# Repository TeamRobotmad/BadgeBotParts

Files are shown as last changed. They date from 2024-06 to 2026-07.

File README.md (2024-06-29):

# BadgeBotParts
Related documents and CAD files for BadgeBot - a small robot based on the [EMF Camp 2024 Badge](https://tildagon.badge.emfcamp.org/)

Buy at https://robotmad.odoo.com/

The motors, wheels & ball caster come from [Pololu](https://www.pololu.com), available from other ditributors as well like [Technobots](https://www.technobots.co.uk) and the [PiHut](https://thepihut.com).
+ https://www.pololu.com/product/952
+ https://www.pololu.com/product/1088
+ https://www.pololu.com/product/1098

# Hexpansion EEPROM Recovery #
If you have issues with any hexpansion which contains an app on its EEPROM causing the Badge S/W to crash you can erase the EEPROM by following the instructions in [hexpansion_eeprom_recovery](https://github.com/TeamRobotmad/BadgeBotParts/blob/main/Docs/hexpansion_eeprom_recovery.pdf)

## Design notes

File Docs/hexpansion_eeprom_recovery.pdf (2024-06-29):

### emfcamp/badge-2024 Hexpansion EEPROM Recovery

If you have issues with a HexDrive, or for that matter any hexpansion fitted with an EEPROM, e.g. a software incompatibility with a particular badge software version, you can reset the EEPROM back to blank as follows:

1. Plug in the hexpansion to Slot 1 (will work with any slot but you have to change the "1" below to the slot number.
2. Connect your favourite Terminal program to the COM port presented by the Badge over USB.
3. Press "Ctrl" & "C" simultaneously. i.e. "Ctrl-C"
4. You should now be presented with a prompt ">>>" which is called the python REPL. At this type in the following lines (the HexDrive EEPROM is 8kbytes so requires 16 bit addressing, hence the addrsize=16 other hexpansions may use smaller EEPROMS where this is not required):

from machine import I2C
i = I2C(1)
i.writeto_mem(0x50, 0, bytes([0xFF]*8192), addrsize=16)
5. As long as there is no Traceback then this worked. But you can check by reading back the EEPROM contents with:

i.readfrom_mem(0x50,0,32,addrsize=16)

You should get a response which confirms that the first 32 bytes have been reset back to 0xFF:
b'\xff\xff\xff\xff\xff\xff\xff\xff\xff\xff\xff\xff\xff\xff\xff\xff\xf f\xff\xff\xff\xff\xff\xff\xff\xff\xff\xff\xff\xff\xff\xff\xff'

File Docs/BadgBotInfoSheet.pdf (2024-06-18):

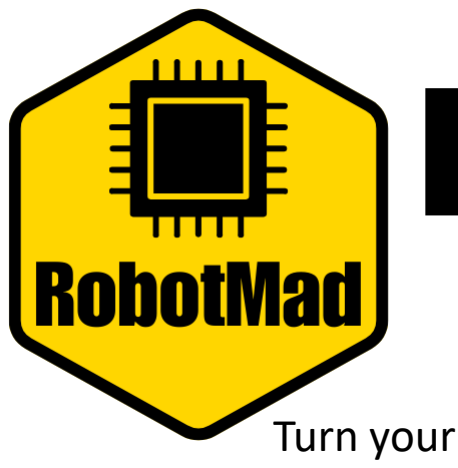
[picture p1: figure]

# BadgeBot

Turn your EMF 2024+ Badge into a Robot!

Using the RobotMad Hex-Drive Hexpansion, and 3D
printed motor mounts.

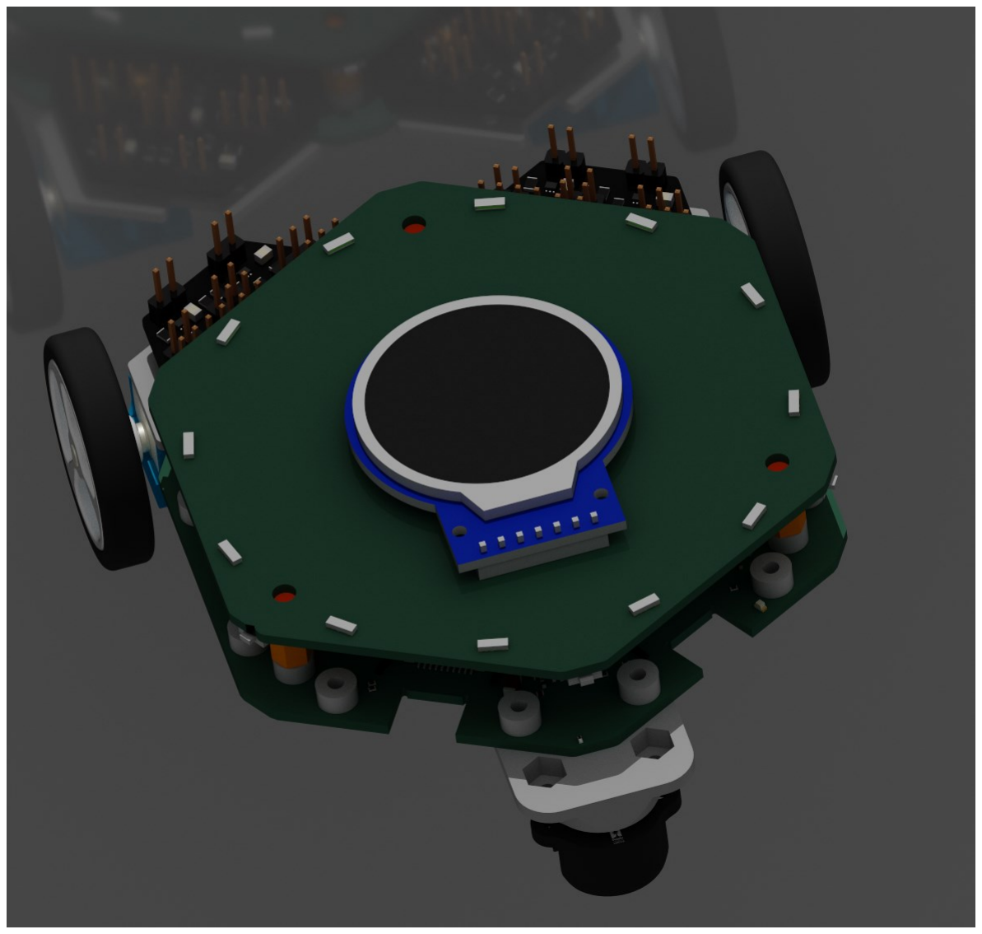
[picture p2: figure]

Designed for n20 micro gear motors, Pololu 32mm wheels, and ball caster.

https://www.pololu.com/category/60/micro-metal-gearmotors

https://www.pololu.com/product/952 https://www.pololu.com/product/1088

Mount the system to the underside of your badge using one pair of m2 mounting holes, pair A for the motor pointing straight out the side. Pair B or C for angled motor mounting, this will include one of the motor mount top part holes and will need a longer m2 bolt.

| Here is an example of a motor mount set up using the C pair of holes lined up with the expansion mounting holes of the badge, while one bolt also holds the mo- tor mount.

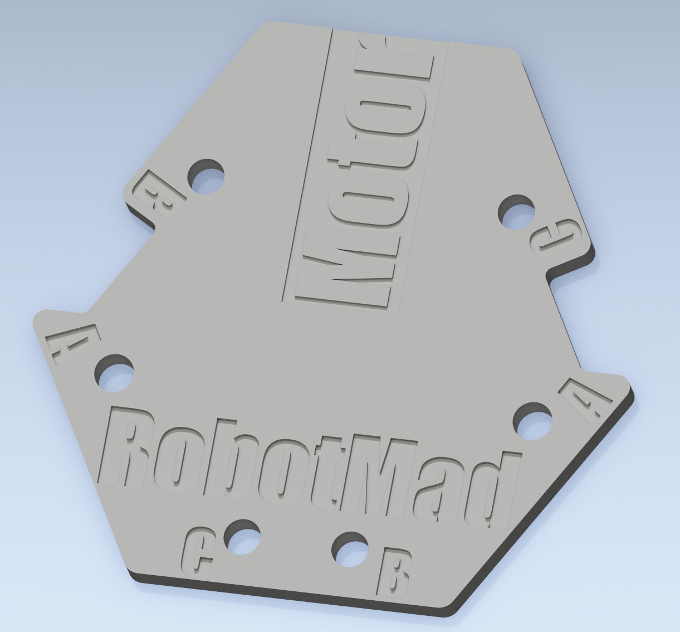
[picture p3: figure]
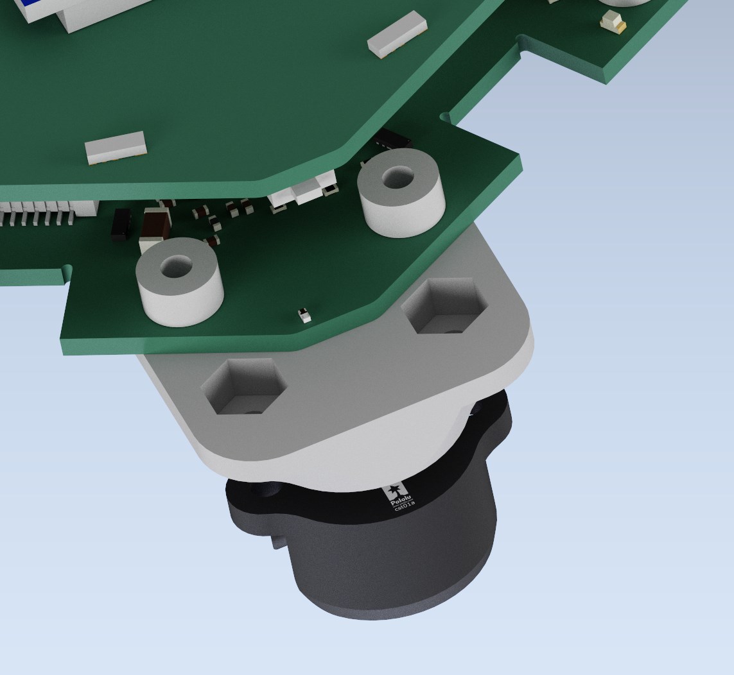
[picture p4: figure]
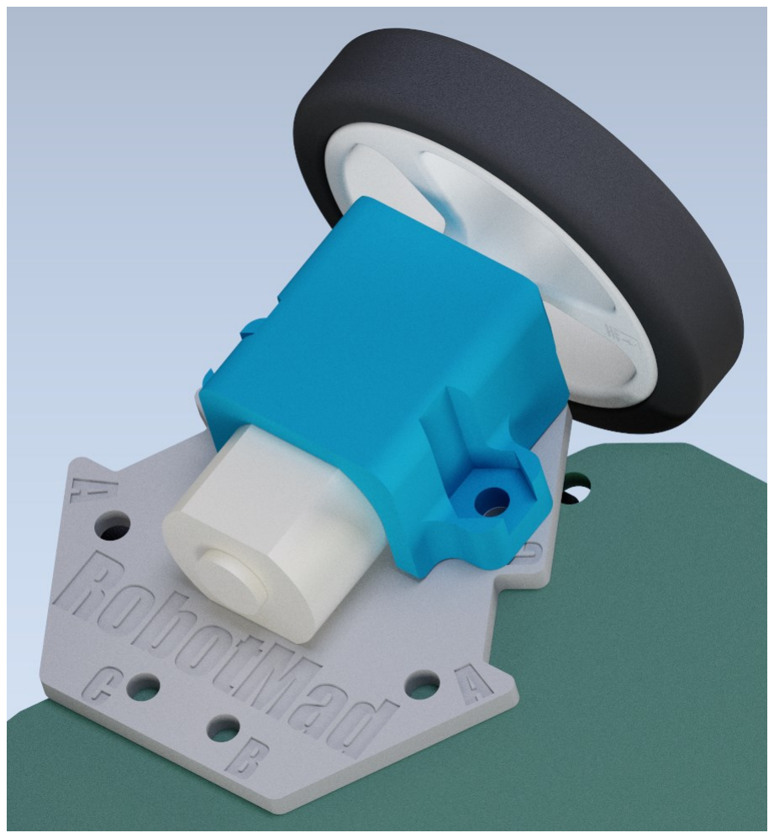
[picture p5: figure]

The ball caster mounts across a corner of the badge using the adjacent hexpansion mounts.

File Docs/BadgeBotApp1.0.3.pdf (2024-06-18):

BadgeBot App V1.0.3 Instructions.

For use with Badge FW 1.7.0 (follow official guidance to update and connect to home network Wi-Fi https://tildagon.badge.emfcamp.org/using-the-badge/end-user-manual/)

Install on the Badge via options—App store, StoreInstall, BadgeBot.

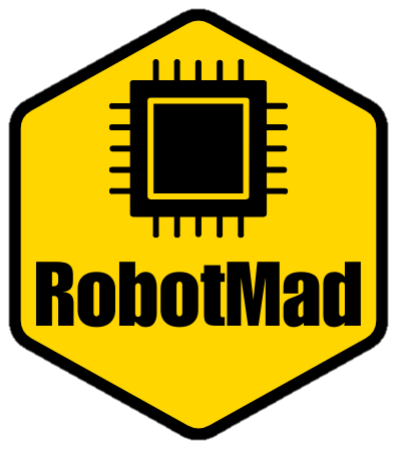
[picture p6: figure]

Navigate to BadgeBot app, On the first time run expect to need to flash the EEPROM on the Hex-Drive hexpansion.

This allows the hexpansion to be automatically recognised. This means you need to not have any other hexpansions plugged in to your badge during the EEPROM flashing process. If built the same as BadgeBot instructions the HexDrive hexpation should come up as in slot 3, with the BadgeBot app giving the following message. “Hexpansion Detected in (Slot 3) init EEPROM as HexDrive”

Press C to accept.

Next the app will prompt to install the Hex-drive app onto the hexpansion,

“HexDrive detected in Slot 3, Upgrade HexDrive App?”

Press C to accept. The app will then need you to “reboop” your badge using the button on the base badge board, labelled on the underside. The first time set-up is now complete.

Navigate back to the BadgeBot app.

The app will tell you to press C to begin programming your movement sequence.

Create your program using buttons A, B,D, and E.

Run using a long press of button C.

Set the badge down during the 5 second count down and watch it go!

After the program has run you can run the same program again by pressing C or restart the programming process using F.

Enjoy experimenting with the movement program.

The App code is open source on GitHub, try adding your own functionality!

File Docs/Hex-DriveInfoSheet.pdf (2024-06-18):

# RobotMad Hex-Drive

A Motor and servo drive hexpansion for the EMF Badge.

## Featuring:

### 3 power source options

### 2 Motor drivers

### Up to 4 servo outputs

### Adjustable 5V power supply

### (max 12v)

### 64K bit EEPROM

### Easy to modify 0805 based design

## Power Options

The Hex-Drive supports badge supplied power, 1 cell external battery, or 2 cell external battery.

Badge power is selected by default using a copper track on the back of the board.

To select an external power source, the track between +BADGE and +LV must be cut carefully along the line indicated “CUT” between the white marked lines.

Then using header pins and a jumper connect +BAT to +LV for a 1 cell battery, or +BAT to +HV for a 2 cell battery. The battery should be connected to the BAT pins just to the side of the selector pins. TAKE CARE ABOUT POLARITY

You can return to Badge supplied power by connecting +BADGE to +LV again.

## Motors and Servos

There are 2 separate motor drivers and outputs. M1, M2.

4 servo outputs, S1, S2, S3, S4.

All of these outputs accept standard 2.54mm pitch header pins

To use a servo you have to not be using its corresponding motor. S1 and S2 correspond to M1, S3 and S4 correspond to M2.

If only using motors, it is beneficial to add some large though hole capacitors to the board using the servo power connection

## Adjustable Power supply

The power supply is adjustable by changing the feedback voltage divider resistors R1 and R2. we recommend only changing R2, changing C2 and C3 is recommended when changing voltage. Additional capacitors added to power points on the board is always beneficial to voltage stability.

When on badge power current limit is 300mA at 5V.

On single cell lipo, max current is 900mA

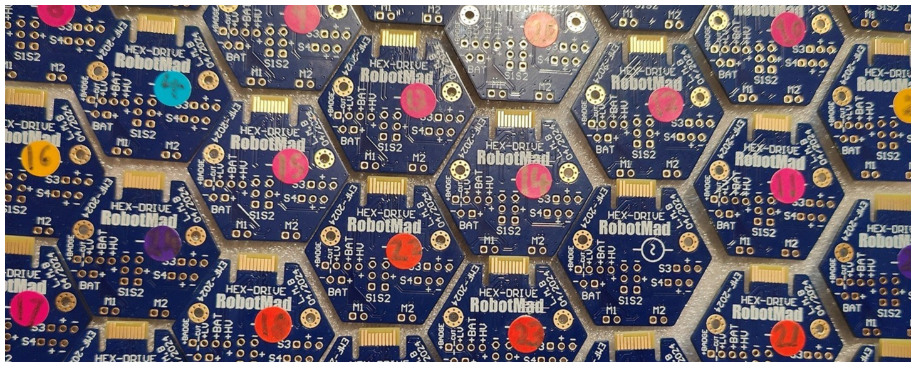
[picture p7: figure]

Below is values for 5V (default), 6V and 12V.

Vout | R2 | C3 | C2
5 | 30k | 1.8nF | 22uF
6 | 37.4k | 1.5nF | 30uF
12 | 86.6k | 560pF | 47uF

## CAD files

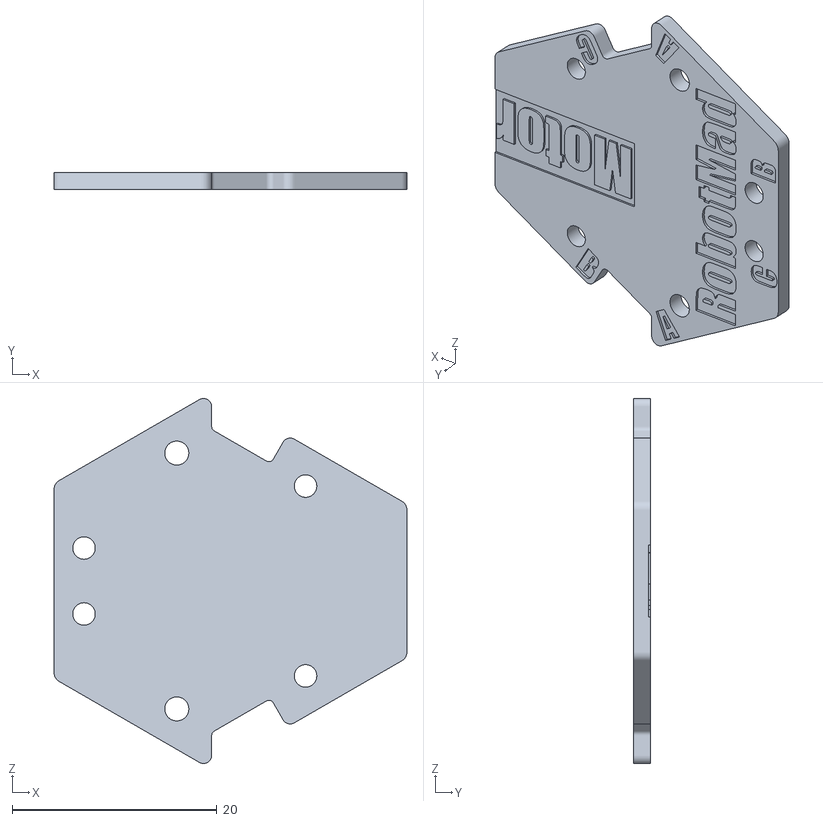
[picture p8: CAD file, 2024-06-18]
STL files/motormountV2.stl
34.5 x 1.70 x 35.7

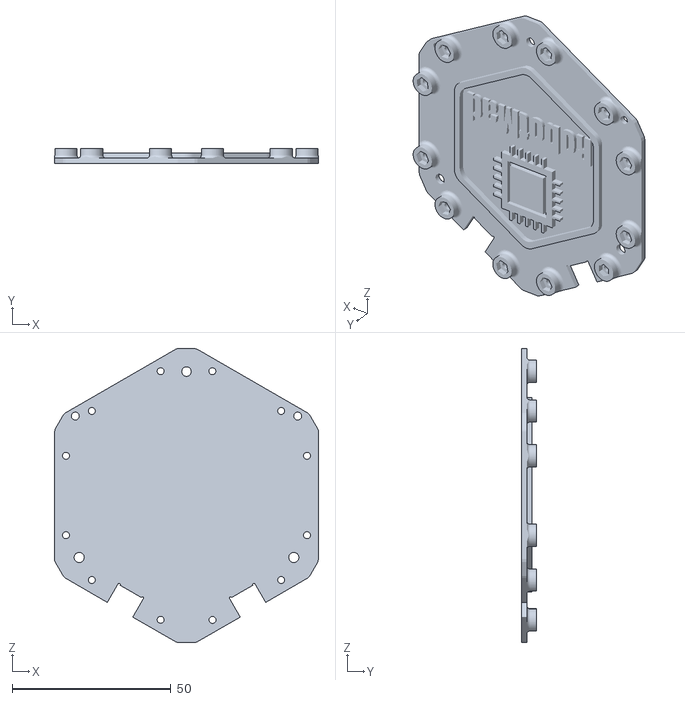
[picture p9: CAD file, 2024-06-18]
STL files/fakebadgeV1.stl
83.1 x 4.60 x 92.5

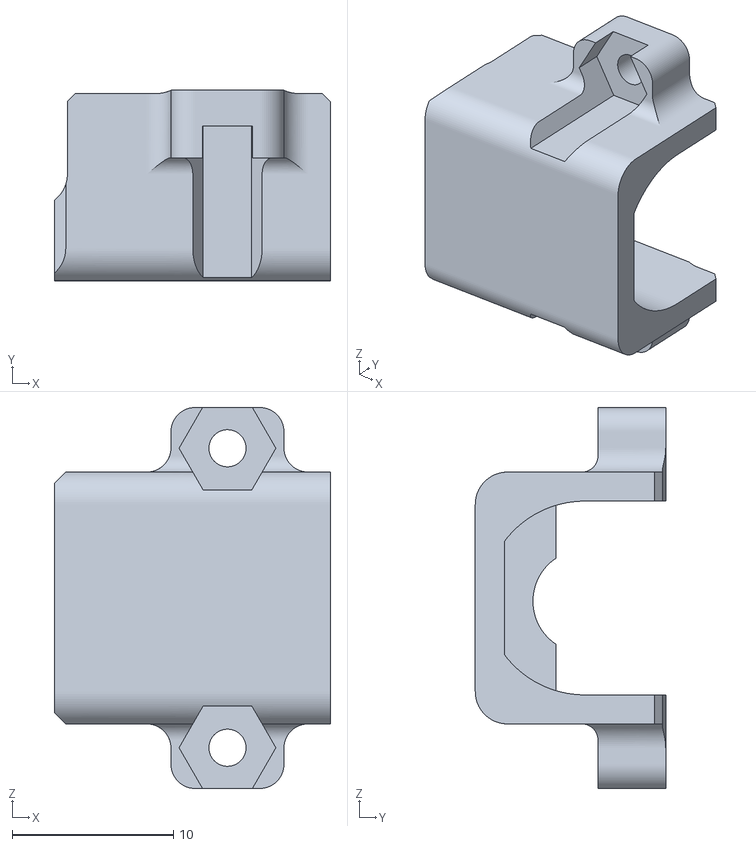
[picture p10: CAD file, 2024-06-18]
STL files/MotorTopV2.stl
17.1 x 11.8 x 23.6

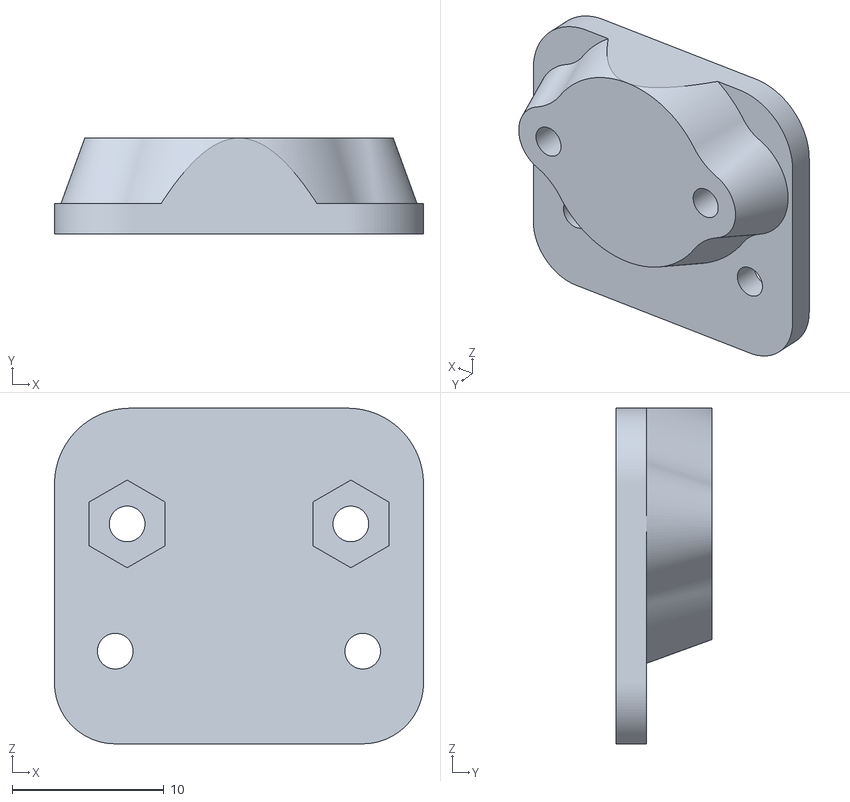
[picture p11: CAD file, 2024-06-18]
STL files/ball-mountV1.5.stl
24.3 x 6.30 x 22.1

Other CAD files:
CAD files/MotorTop.ipt
CAD files/ball-mount.ipt
CAD files/motormount.ipt

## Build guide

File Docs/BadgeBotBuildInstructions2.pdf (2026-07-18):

# BadgeBot Kit Parts list

## HexDrive-V2

1x

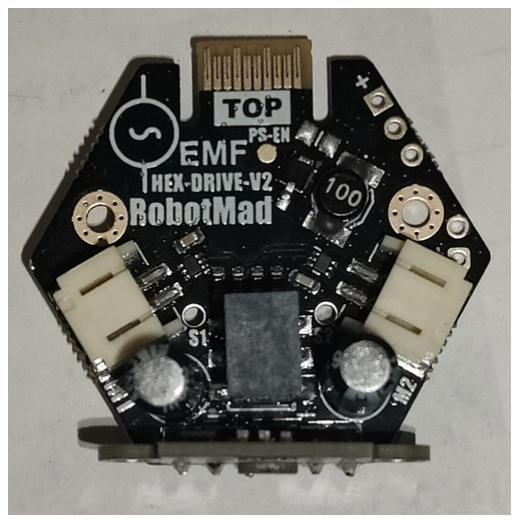
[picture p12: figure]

## LED Shroud

1x

## Short Screw m2-5mm

8x

## Long Screw m2-8mm

2x

## Motor top bracket

2x

## Mounting plate

2x

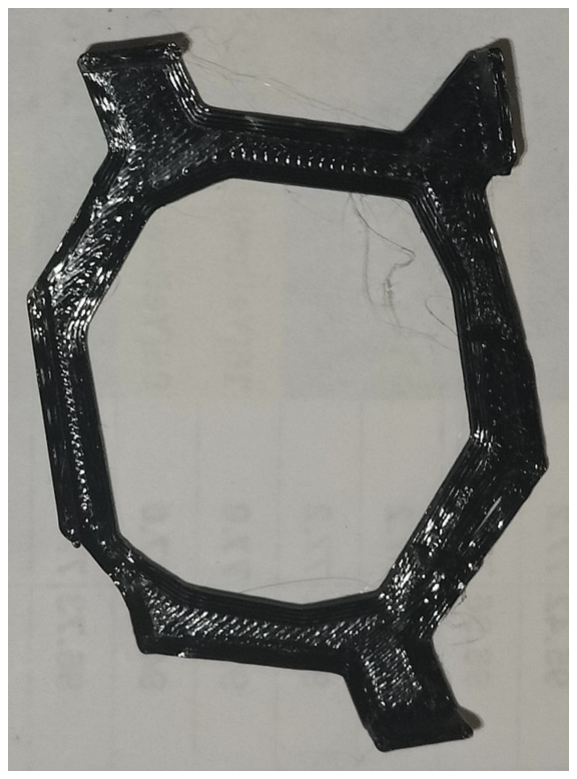
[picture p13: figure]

## Motor

2x

## Left – Yellow & Orange Right – Blue & Green

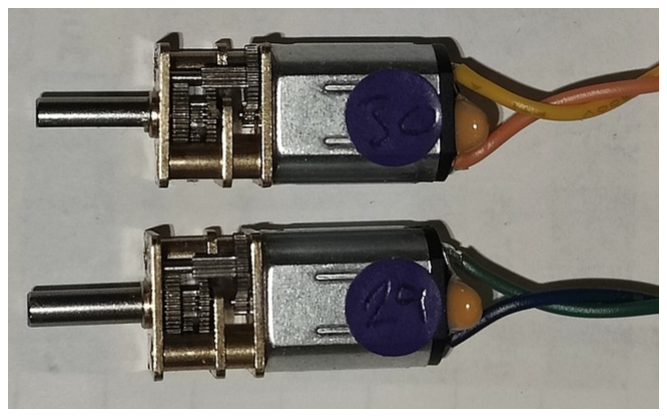
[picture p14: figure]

## Cable Clip

1x

## Free Gift, Badge Battery holder - 1x

## Nut m2

2x

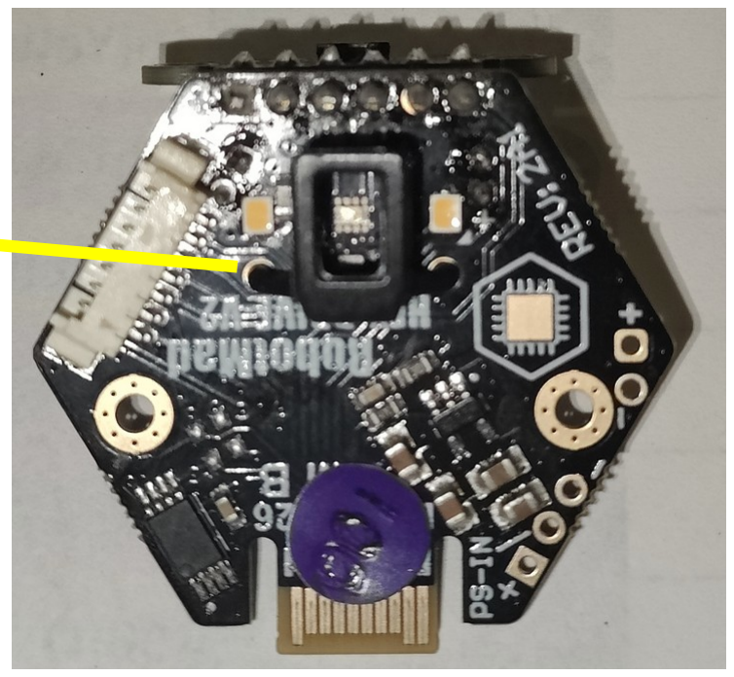
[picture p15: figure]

1. Insert the small ‘LED shroud’ piece into the 2

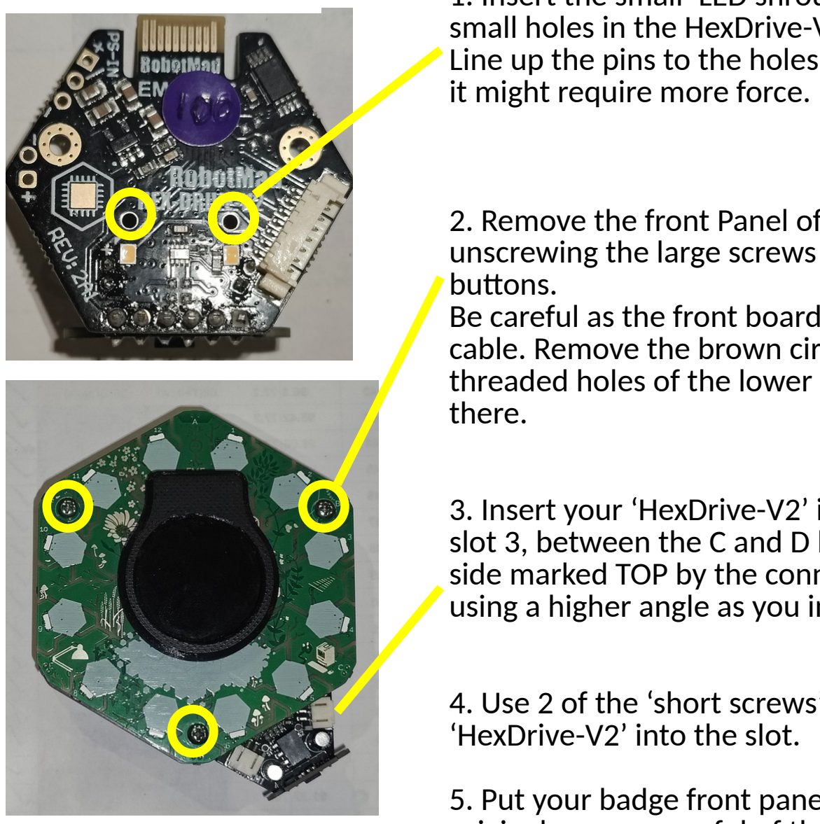
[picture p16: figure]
it might require more force.; buttons.; there.; ‘HexDrive-V2’ into the slot.

small holes in the HexDrive-V2, facing the front. Line up the pins to the holes and push carefully but

2. Remove the front Panel of your badge by unscrewing the large screws by the B, D, and F
Be careful as the front board is still attached via flex cable. Remove the brown circles covering the threaded holes of the lower board if they are still

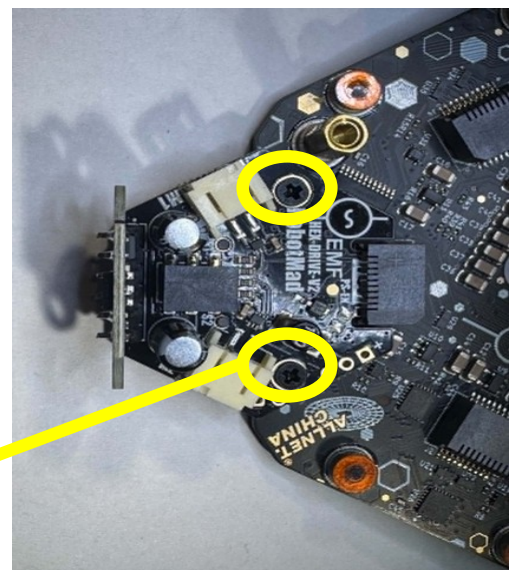
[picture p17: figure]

3. Insert your ‘HexDrive-V2’ into the hexpansion slot 3, between the C and D buttons. Make sure the side marked TOP by the connector is facing up. Try using a higher angle as you insert into the slot.
4. Use 2 of the ‘short screws’ to secure the

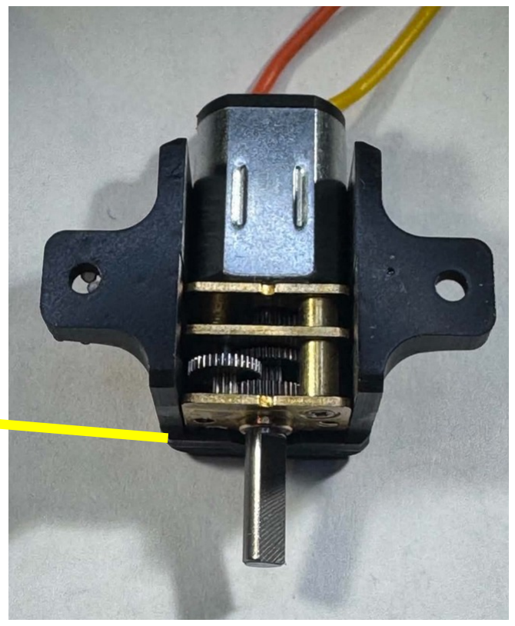
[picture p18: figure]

5. Put your badge front panel back on using its original screws, careful of the flex cable.
6. Turn your badge over, careful of the screen.
7. Line up one of the ‘mounting plates’ to the badge over the slot to the left of the ‘Hex-Drive-V2’. Use a ‘short screw’ in the hole labelled L into the hole closer to the ‘HexDrive-V2’.
8. Place the ‘motor’ with the orange and yellow wires, inside the ‘motor top bracket’ with the gearbox up against but inside the small wall at one end.
9. Place the ‘motor top bracket’ with the ‘motor’. Over the raised platform of the ‘mounting plate’ Matching and lining up with the ML and MR holes.
10. Screw a ‘long screw’ though the hole marked ML, though the ‘motor top bracket’, ‘mounting plate’ and into the badge’s other mounting hole for this hexpansion slot.

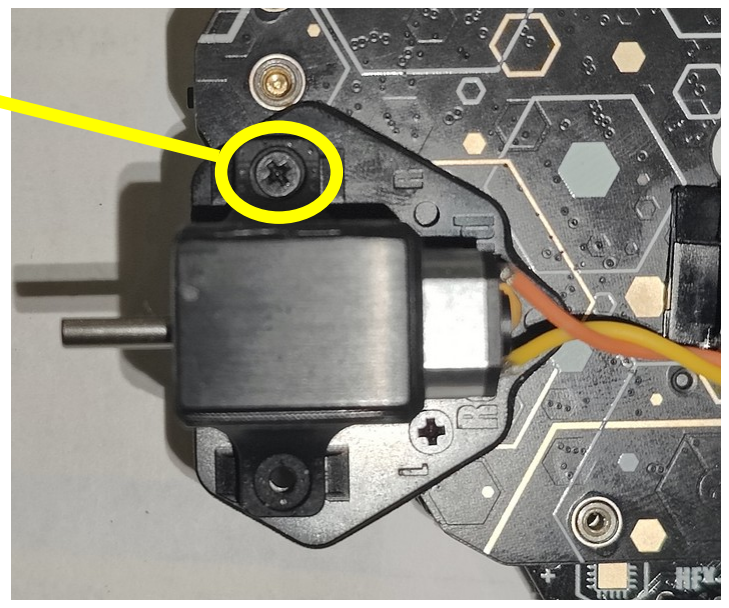
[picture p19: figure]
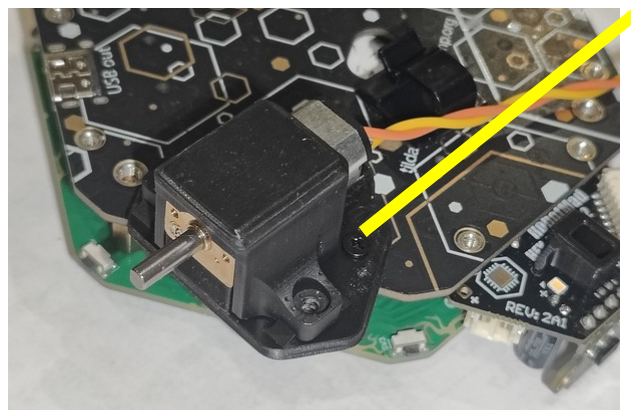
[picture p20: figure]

11. Use a ‘short screw’ in the hole marked MR while holding a ‘nut’ on the other side of the ‘mounting plate.’

BadgeBot build instructions.

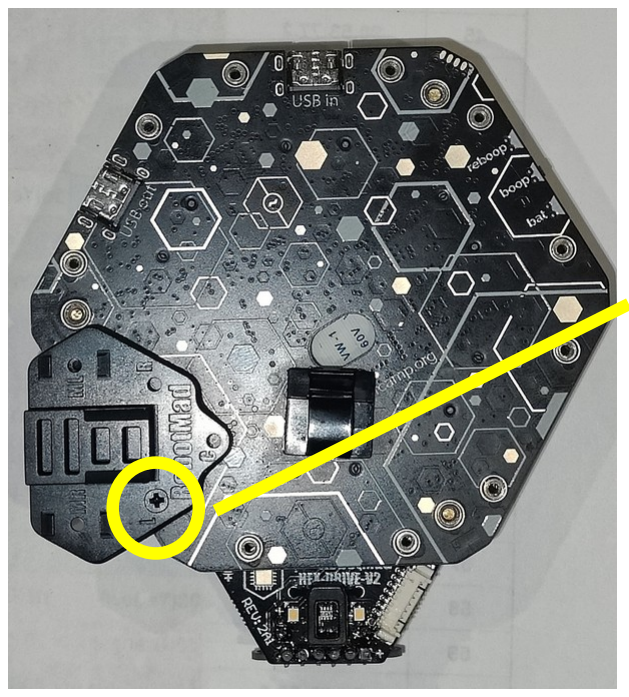
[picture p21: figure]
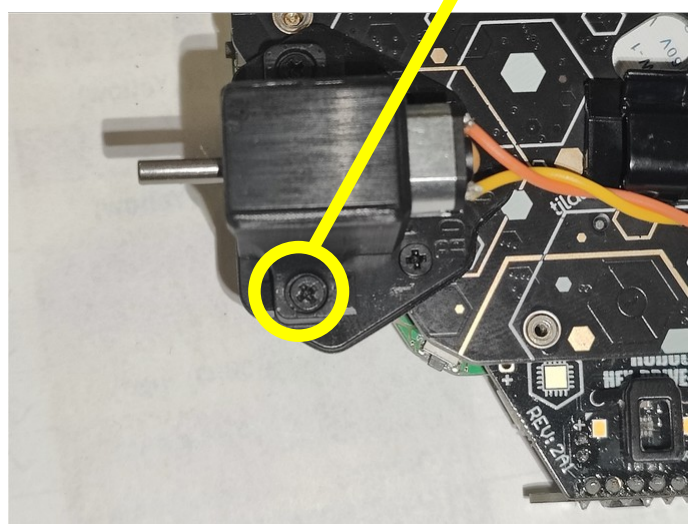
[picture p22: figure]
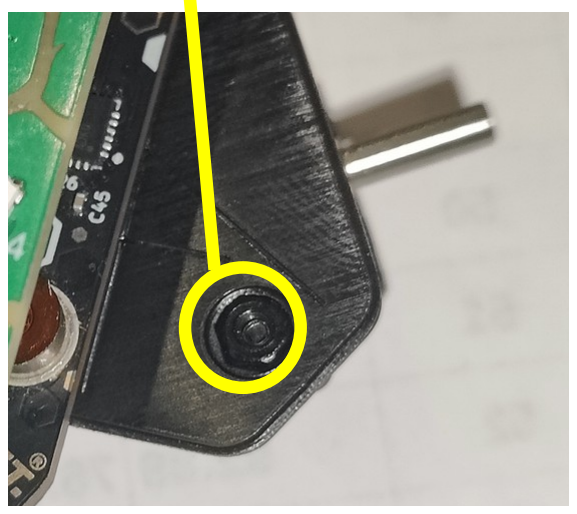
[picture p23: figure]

BadgeBot build instructions.

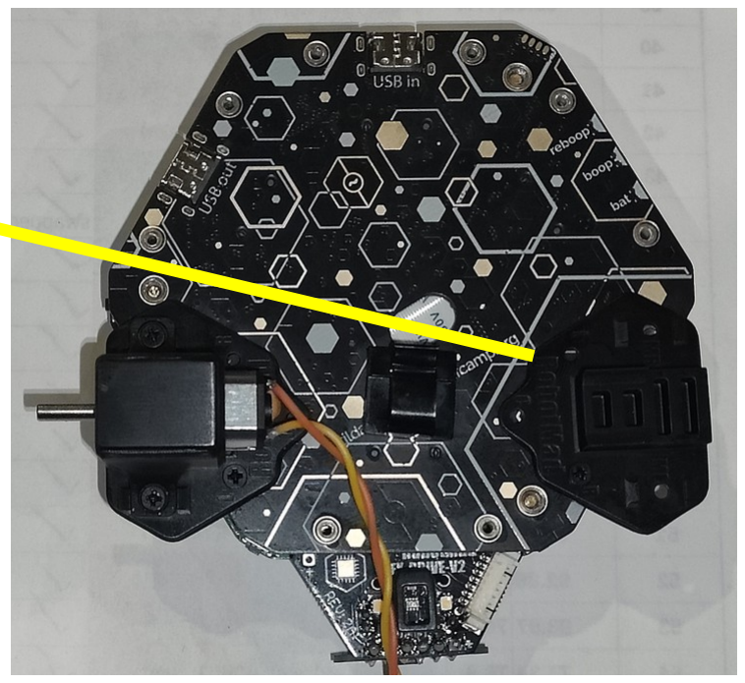
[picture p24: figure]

12. Line up the other ‘mounting plate’ to the badge over the slot to the right of the ‘Hex-Drive-V2’. Use a ‘short screw’ in the hole labelled R into the hole closer to the ‘HexDrive-V2’

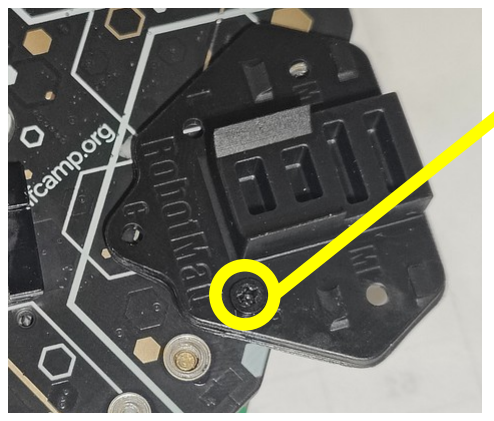
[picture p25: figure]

8. Place the ‘motor’ with the green and blue wires, inside the other ‘motor top bracket’ with the gearbox up against but inside the small wall at one end.

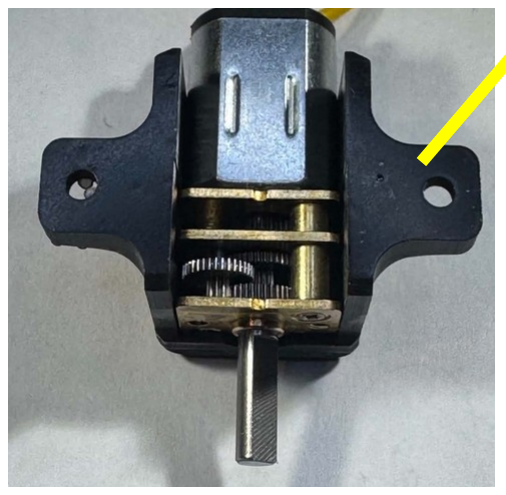
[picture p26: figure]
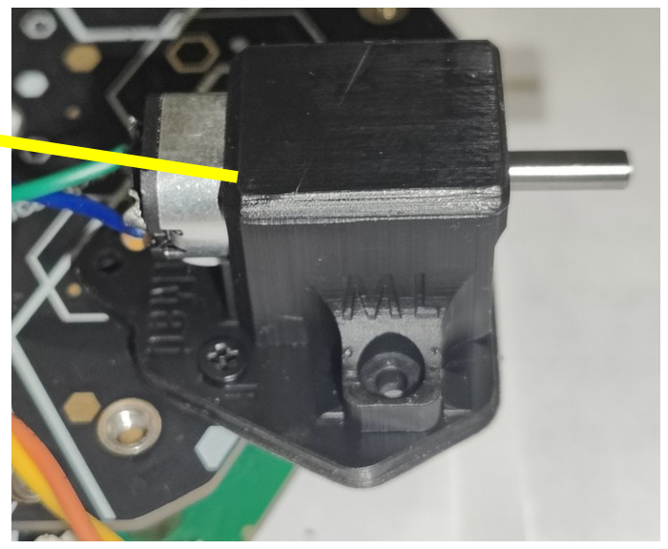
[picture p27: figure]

9. Place the ‘motor top bracket’ with the ‘motor’. Over the raised platform of the ‘mounting plate’ Matching and lining up with the ML and MR holes.
15. Screw a ‘long screw’ though the hole marked MR, though the ‘motor Top bracket’, ‘mounting plate’ and into the badge’s other mounting hole for this hexpansion slot.

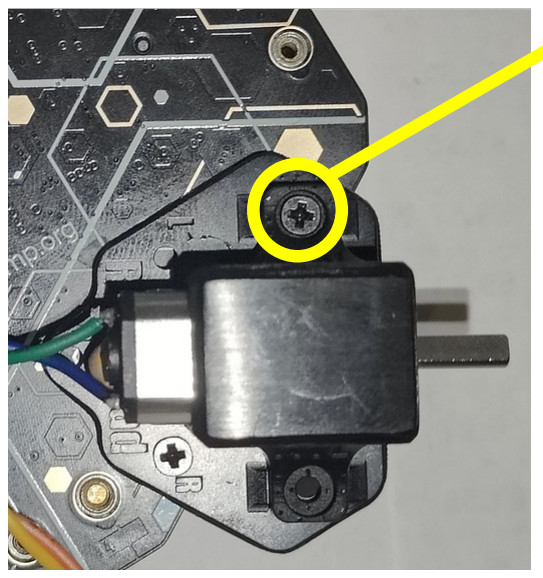
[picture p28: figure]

16. Use a ‘short screw’ in the hole marked ML while holding a ‘nut’ on the other side of the ‘mounting plate’.
17. Plug in the ‘motors’ to the ‘HexDrive-V2’ crossing the wires over for the neatest connection. The connectors are rather tight and polarised with a notch at the top. Orange and yellow into ‘M1’. Blue and green into ‘M2’.
18. Take off the backing and place the ‘cable clip’ just above the hole in the badge main board, in line between the 2 motors. Then insert the wires from the motors to keep them tidy.
19. Use 2 ‘small screws’ in the holes on the ‘ball mount’ marked S, lined up to the holes of the hexpantion slot between buttons F and A. Under the USB in port.

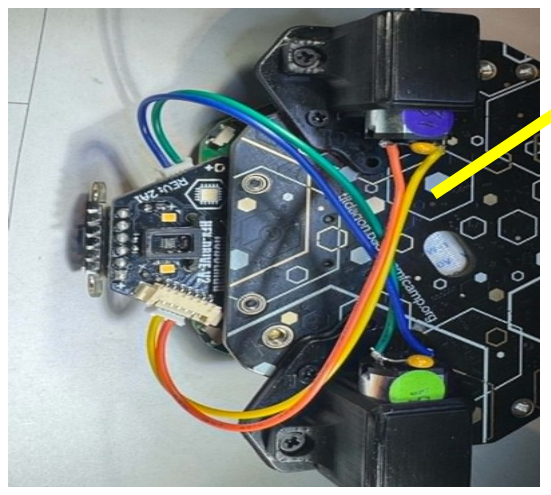
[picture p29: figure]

20. Push the ‘wheels’ onto the motor shafts, flat side out, by lining up the flat side of the shaft with the flat in the wheels hole.

Your BadgeBot is complete! You can now install the BadgeBot app from the Badge’s app store.

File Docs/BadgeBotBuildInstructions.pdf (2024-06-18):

BadgeBot build instructions.

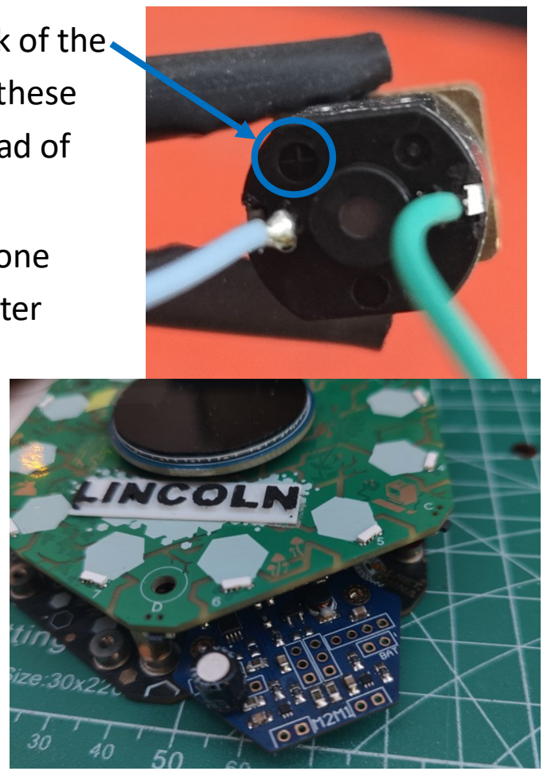
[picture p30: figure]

1. Solder wirers to the motors. Notice the + mark on the back of the motor. Colour coded in these instructions for connivance as these do matter ort your robot may go backward or in circles instead of forwards.

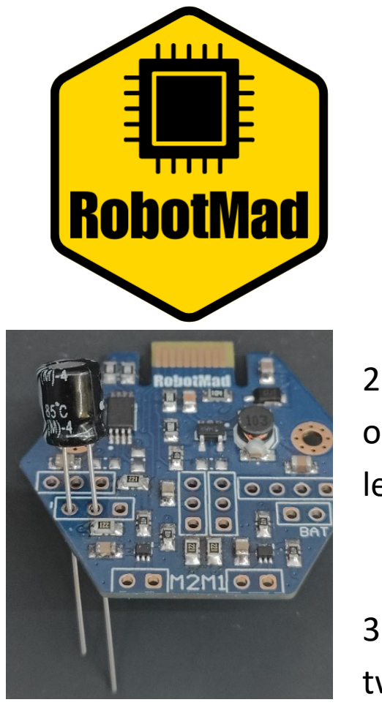
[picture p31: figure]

2. Solder the optional but recommended additional capacitor to one of the servo outputs. Note the polarity, grey line on cap and shorter leg go to the negative marked hole.
3. Insert the HexDrive hexpansion into the slot on the badge between the C and D buttons.

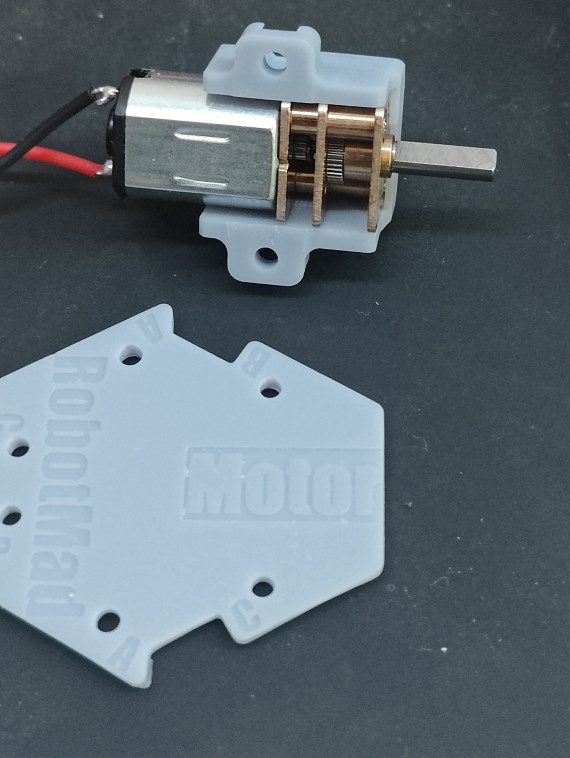
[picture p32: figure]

4. Insert the motors into the motor mounting pieces. Then place on the mounting bracket over the “Motor” text.

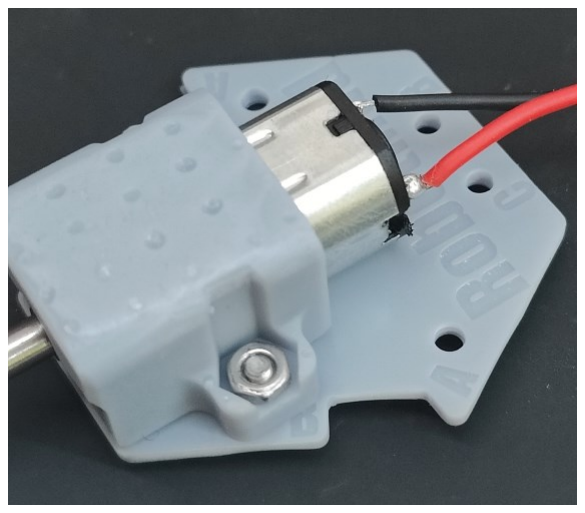
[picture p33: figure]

5. bolt the motor down using a small m2 bolt and nut, though the ‘B’ hole. Do not do the other side of the motor mount yet.

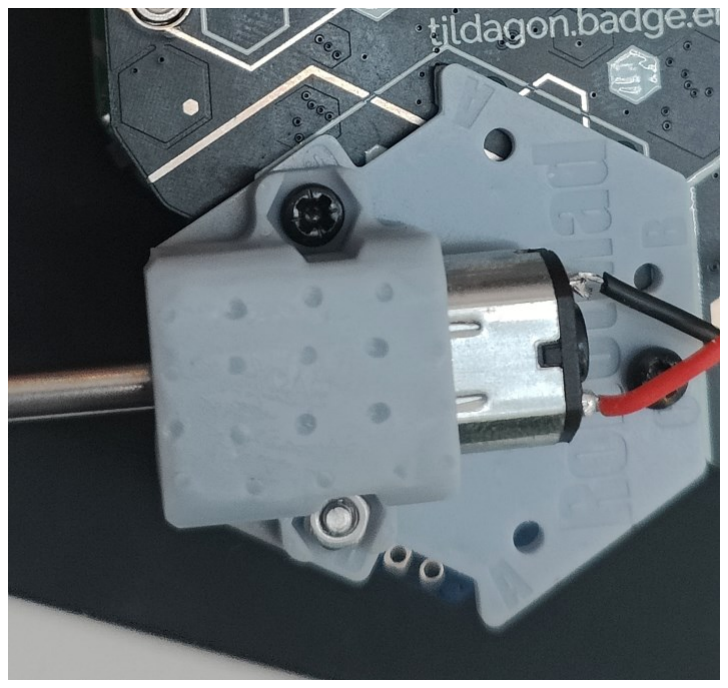
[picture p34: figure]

6. Place the motor bracket on the back of the badge, over the hex-drive, with motor axel pointing out to the side. Line up hole C with the hexpansion port threaded hole in the badge and bolt using a short m2 bolt.
7. Now thread in the longer m2 bolt to the other motor mount hole, all the way though into the threaded hole of the badge. Double check the hexpansion is all the way into its slot or the bolt may hit it.

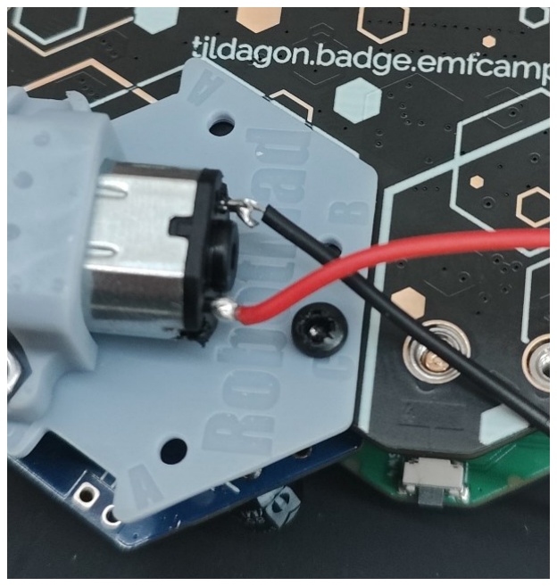
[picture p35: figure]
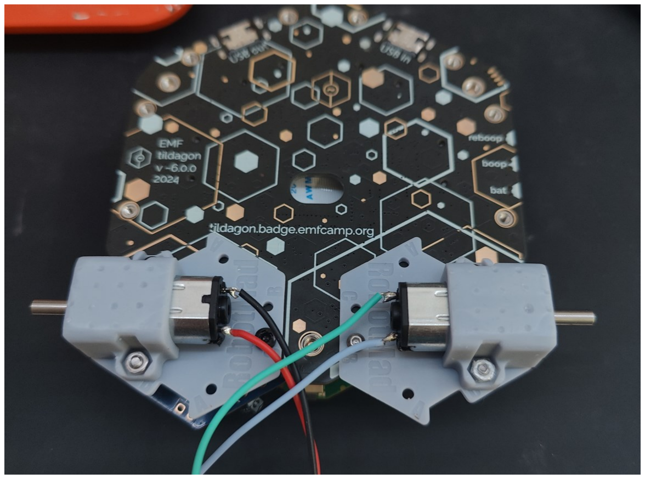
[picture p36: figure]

8. Repeat steps 4 to 7. mounting the second motor across from the first. Using the other holes, so C instead of B and B instead of C.

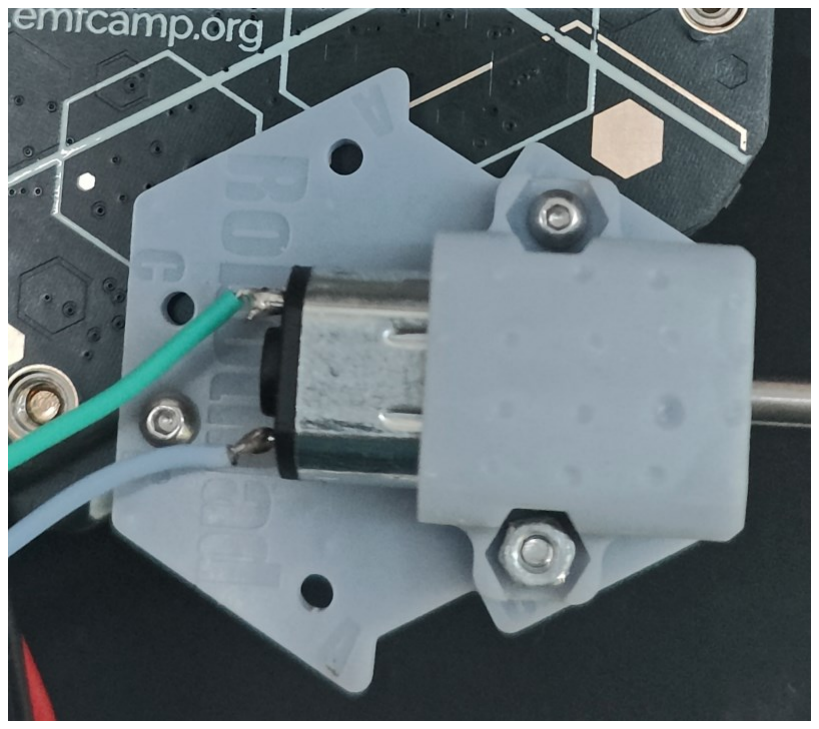
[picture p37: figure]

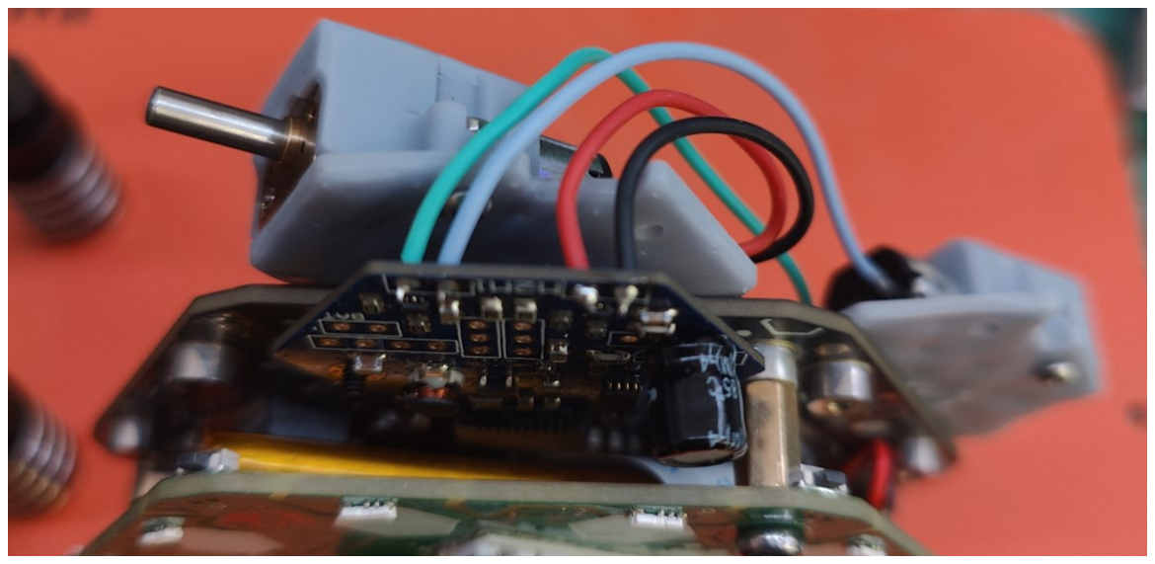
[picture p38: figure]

9. Solder the motor wires to the HexDrive by inserting though the holes marked
M1 and M2, from the under side then solder on the top side.

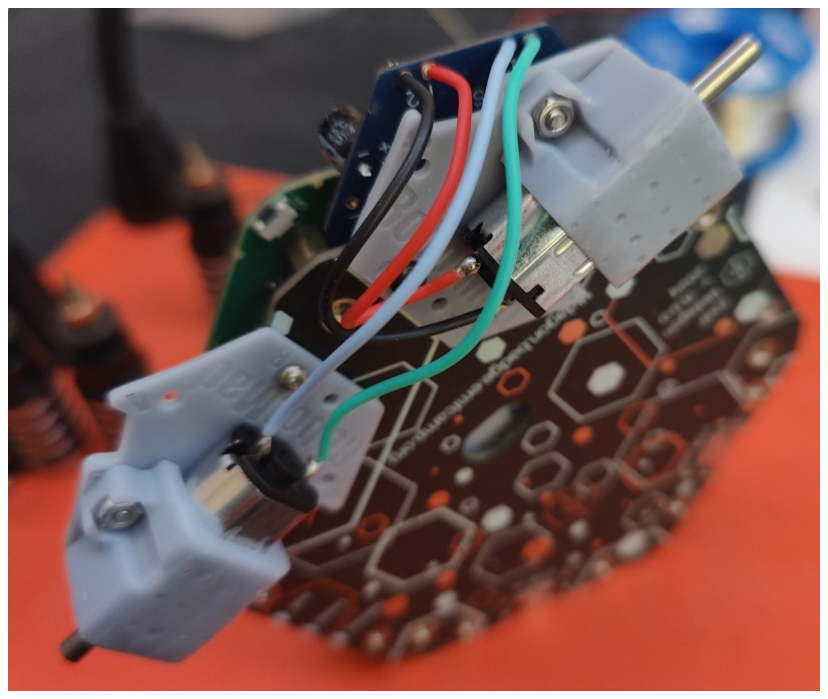
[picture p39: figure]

Please follow the wiring shown in the pictures or your BadgeBot may go in the wrong direction or only spin in circles. The wires are colour coded in these instruction but yours do not need to be.

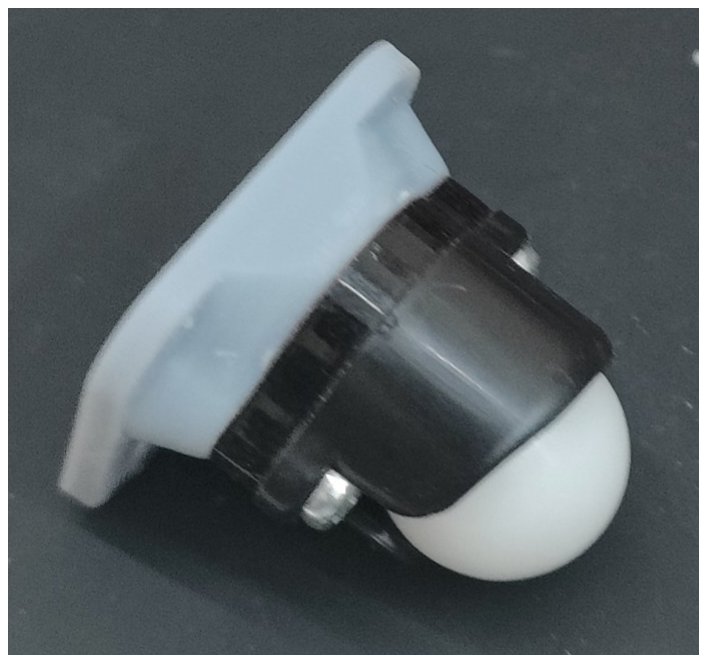
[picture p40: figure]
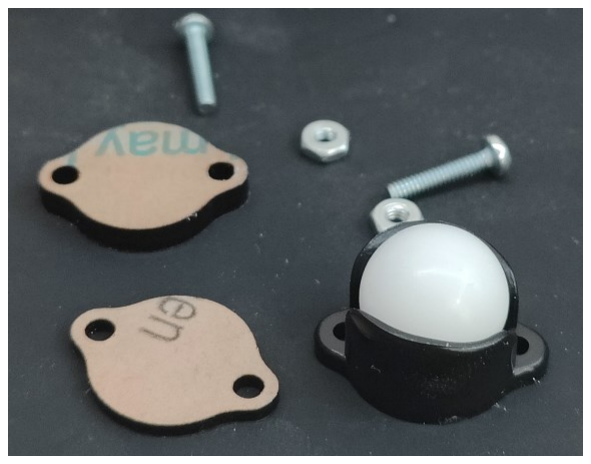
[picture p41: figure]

10. The ball caster comes with 2 spacers and 2 bolts and nuts (Not the same as M2). Mount the ball caster to the ball caster mount with the ticker of the 2 spacers, and the included bolts and nuts.

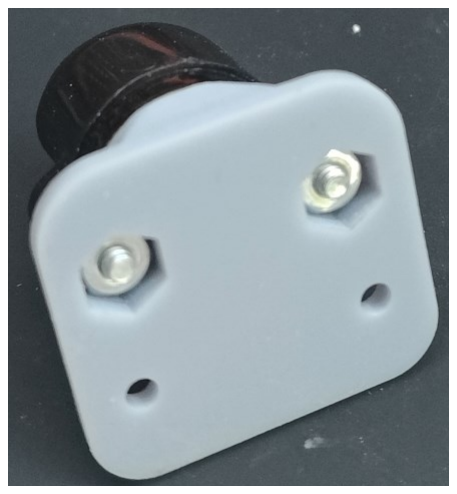
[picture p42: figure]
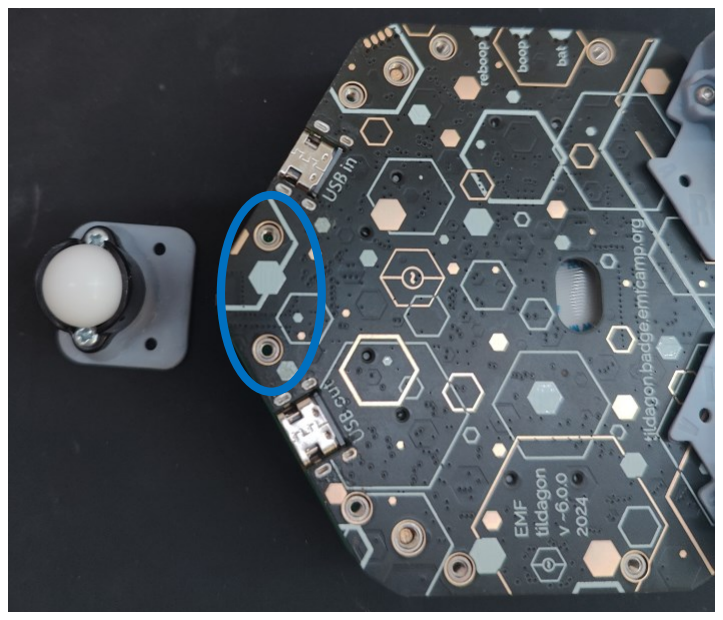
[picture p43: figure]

11. Bolt the ball caster mount to the badge on the corner between the 2 USB ports. Using threaded mounting holes from the hexpansion ports either side. Using 2 short m2 bolts.

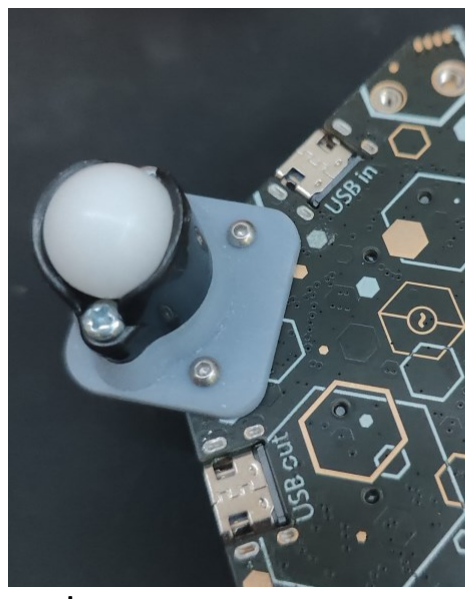
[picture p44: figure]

12. Work the tyres onto the wheels, then put the wheels onto the motor shafts.

The wheel hub as a side that sicks out, this side goes towards the motor.

Watch for the flat side of the shaft to match up, it can take quite a bit of force so brace against the back of the motor to avoid braking the mounts.

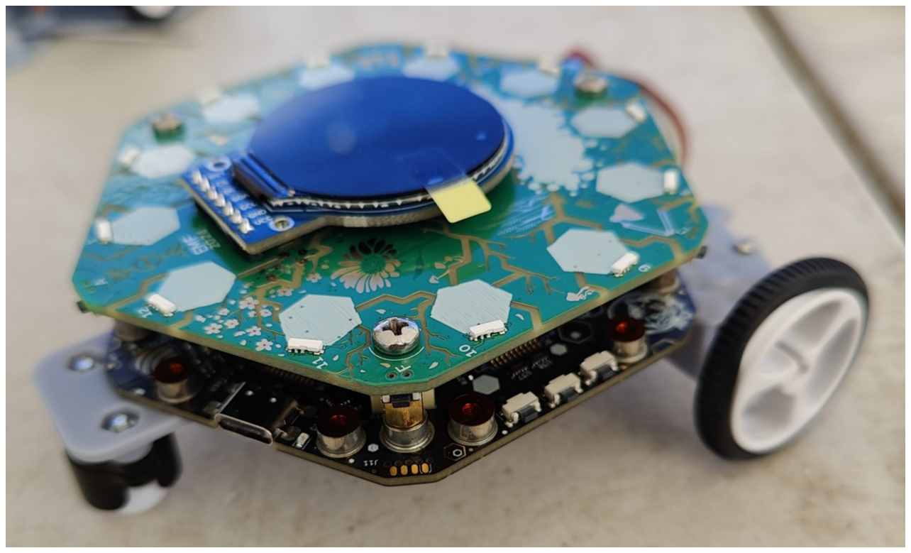
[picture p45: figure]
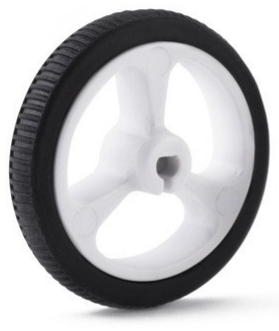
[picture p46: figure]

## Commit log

2024-06-18 add document PDFs and STL files
    [MotorTopV2.stl, ball-mountV1.5.stl, fakebadgeV1.stl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]
2024-06-18 reorganise files and add cad files
    [MotorTop.ipt, MotorTopV2.stl, ball-mount.ipt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]
